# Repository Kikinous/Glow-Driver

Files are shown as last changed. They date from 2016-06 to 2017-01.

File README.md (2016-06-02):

# Glow-Driver
Glow Driver for model engine with current sensor

Blog thread: http://www.eevblog.com/forum/projects/improving-glow-plug-drive-design-for-rc-plane-radial-engine/

* eagle file
  - digikey bill of material
  - OSH park PCB manufacture details

* attiny code
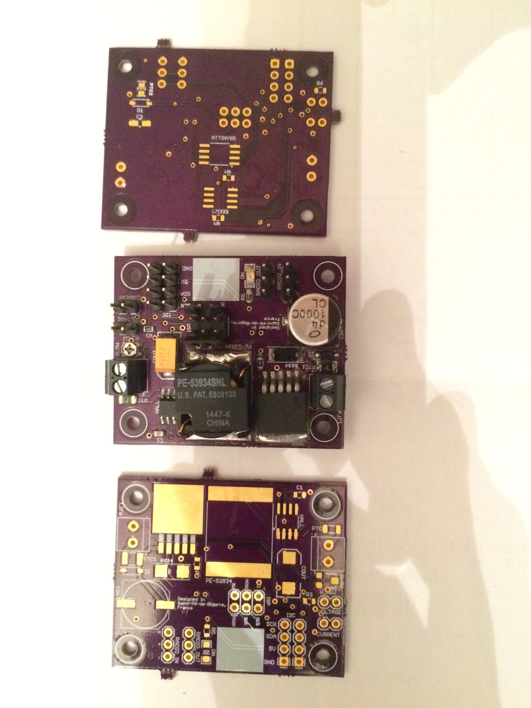
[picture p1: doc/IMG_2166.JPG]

* Main computer board
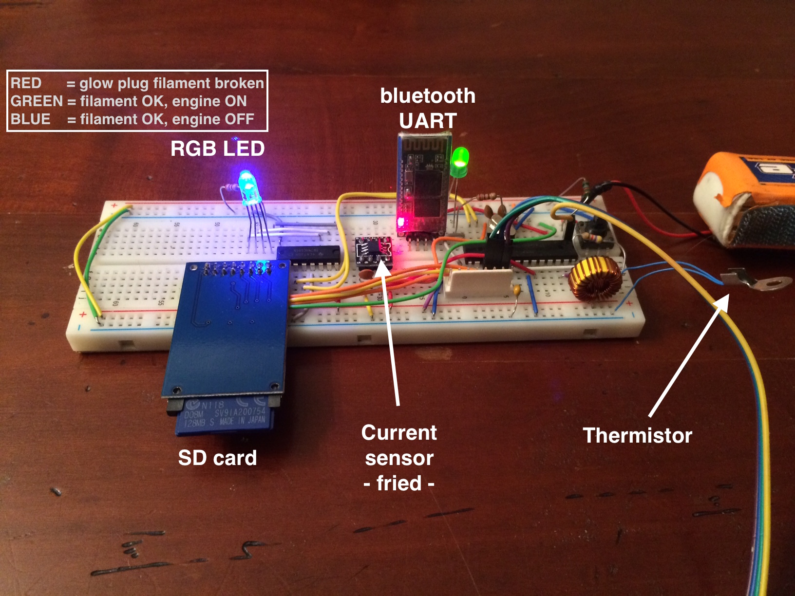
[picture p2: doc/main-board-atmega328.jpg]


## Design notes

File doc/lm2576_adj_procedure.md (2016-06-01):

# LM2576-ADJ

# Given
Vout = 1.5V
Vin = 9.9V
Iload = 1.5A (Rload = 1 ohm)

#Programming output voltage
Vout = Vref ( 1+R2/R1) Vref = 1.23V

R2 = R1 (Vout/Vref -1) avec 1k < R1 < 5k
pot : R2 + R1 = 10k
R1 = 8.2k
R2 = 1.8k

# induductor selection
* E.t
E.t = (Vin-Vout)*(Vout/Vin)*(1000/52)  
E.t = (9.9-1.5)*(1.5/9.9)*(1000/52)  
E.t = 24 V/us
* figure 27
E.t = 24 & I = 1.5A => L = 47 - 68 uH
inductance choisie 64uH 5A

# output capacitor
Cout > 13,300 * Vin /(Vout * L[uH]) [uF]
but may be much larger
Cout > 13,300 * 9.9 /(1.5  * 64) [uF]
Cout > 1372 uF
J'avais 680uF, je mets 2000uF

##################################################################

LM2576 - LM2577 up converter : error

# Distronics : TO220-5 LM2596T-ADJ 
## Programming voltage
E.t = (Vin - Vout - Vsat ) . ( Vout + Vd ) / (Vin - Vsat + Vd) . (1000 / 150) [V.us]
E.t = 9.4 V.us
--> 15uH , inductor code = L34  (check table 3)
L34
L = 15
I = 3.40
Through hole or surface mount

## Output capacitor
C = 10nF tantalium or electrolitic - table 2

## Feedforward capacitor 
C = 10nF ceramic - table 2

## Catch diode
Schottky diodes : 5 A rating 

## Input capacitor 
look for RMS current to avoid heating : big capacitor qui chauffe pas

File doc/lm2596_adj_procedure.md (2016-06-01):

# LM2595-ADJ

# Given
Vout = 1.2V
Vin = 9.9V
Iload = 2.5A (Rload = 0.5 Ohm)

#Programming output voltage
Vout = Vref ( 1+R2/R1) Vref = 1.23V

R2 = R1 (Vout/Vref -1) avec 1k < R1 < 5k
pot : R2 + R1 = 10k
R1 = 8.2k
R2 = 1.8k

# induductor selection
* E.t
E.t = (Vin-Vout-Vsat) * (Vout+Vd)/(Vin-Vsat+Vd) * 1000 / 150kHz  (V.us)
Vsat = 1.16V
Vd   = 0.5V
E.t = (9.9-1.2-0.5) * (1.2+0.5)/(9.9-1.16+0.5) * 1000/150
    = 10.06 (V.us)
* figure 24 : 
L = 15uH et inductor code = L34
brand
Schott / hole    = 67148400   =
Schott / SMT     = 67148790   =
Pulse eng / hole = PE-53934   =
Pulse eng / SMT  = PE-53934-S = digikey# 553-1417-ND = 2.17
 
# output capacitor
* Table 2
  Vout ~ 2V --> 330uF/6.3V AVX TPS Series       = digikey 478-9193-1-ND = 1.8 EUR
                470uF/4V   Sprague 595D Series  = no stock

# Catch diode
SK34 - 4->6 Amp  = digikey SK34A-TPCT-ND = 0.5 EUR

#Input Capacitor (CIN)
1000uF/16V                      = digikey P15087CT-ND = 0.9 EUR

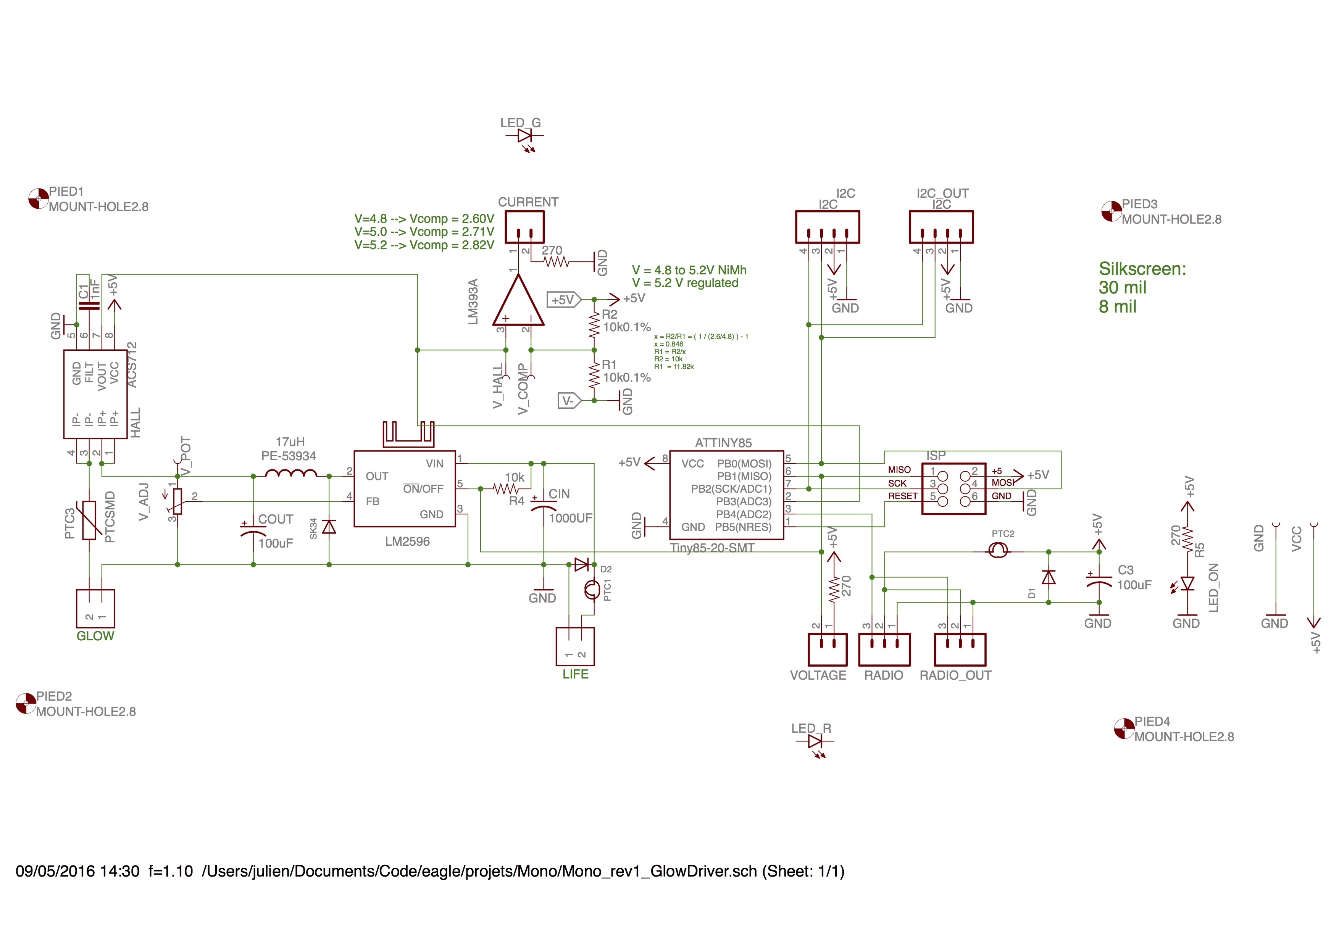
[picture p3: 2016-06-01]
Parts_Manufacture_Orders/Mono_rev1_GlowDriver_schematic.jpg

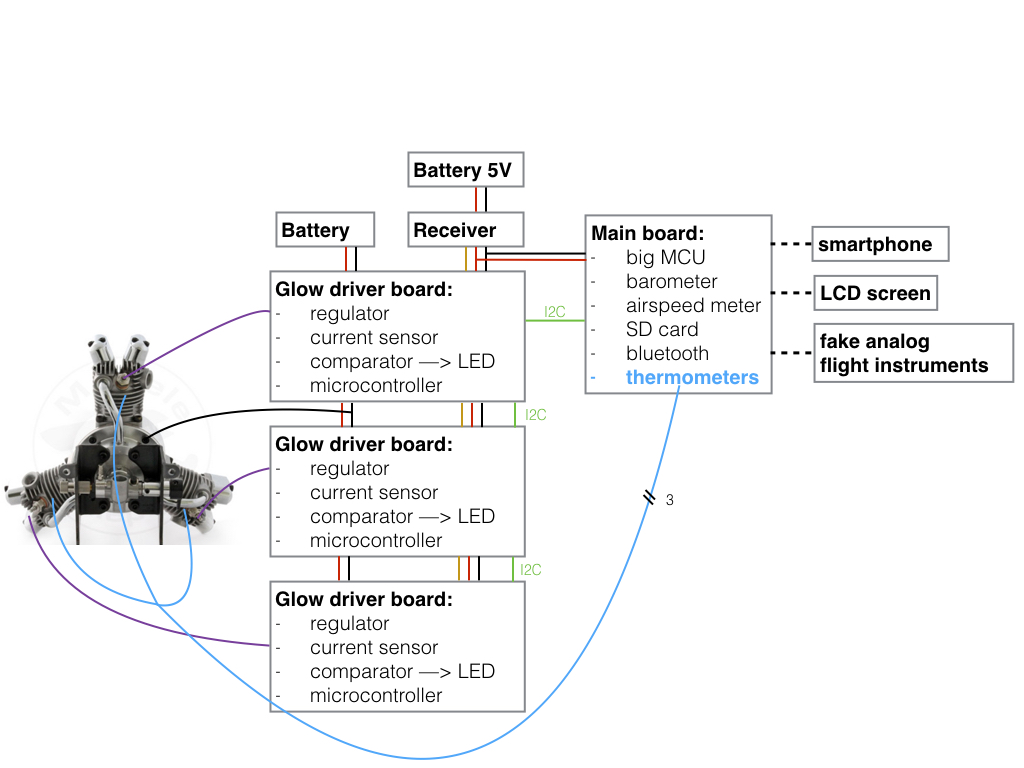
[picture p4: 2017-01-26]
doc/Big-picture.jpg

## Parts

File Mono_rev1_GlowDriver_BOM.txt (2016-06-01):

Partlist exported from /Users/julien/Documents/Code/eagle/projets/Mono/Mono_rev1_GlowDriver.sch at 09/05/2016 11:24

Part      Value                  Device                  Package     Description                                                             DIGIKEY            MF                     MPN              OC_FARNELL OC_NEWARK PROD_ID   VALUE        
ATTINY85  Tiny85-20-SMT          ATTINY45TINY85-20-SMT   SO08-EIAJ   Atmel 8-pin 2/4/8kB flash uC                                            ATTINY85-20SU-ND                                                                IC-09092  Tiny85-20-SMT
C1        1nF                    CAP0805                 0805        Capacitor                                                               490-11585-1-ND                                                                                         
C3        100uF                  CPOL-USCT3216           CT3216      POLARIZED CAPACITOR, American symbol                                    478-1777-1-ND                                                                                          
CIN       1000UF                 CPOL-USG                PANASONIC_G POLARIZED CAPACITOR, American symbol                                    493-3930-1-ND                                                                                          
COUT      100uF                  100UF-10V-10%(TANT)     EIA7343     CAP-07890                                                               478-9193-1-ND                                                                   CAP-07890 100uF        
CURRENT                          M02PTH                  1X02        Standard 2-pin 0.1" header. Use with                                    S1011EC-40-ND                                                                                          
D1                               DIODESOD-123            SOD-123     Diode                                                                   1N4150W-E3-08CT-ND                                                                                     
D2                               DIODESOD-123            SOD-123     Diode                                                                   1N4150W-E3-08CT-ND                                                                                     
GLOW      1X2-3.5MM              1X2-3.5MM               1X2-3.5MM   3.5mm Terminal block                                                    ED1514-ND                                                                                              
GND       TEST-POINTTP_15TH_THRU TEST-POINTTP_15TH_THRU  TP_15TH     Bare copper test points for troubleshooting or ICT                                                                                                                             
HALL      ACS712                 ACS712                  SO08        Hall-effect-based isolated linear current sensor                        620-1189-1-ND                                                                   IC-08964               
I2C       I2C                    M04PTH                  1X04        Header 4                                                                S1011EC-40-ND                                                                                          
I2C_OUT   I2C                    M04PTH                  1X04        Header 4                                                                S1011EC-40-ND                                                                                          
ISP       AVR_SPI_PRG_6PTH       AVR_SPI_PRG_6PTH        2X3         AVR ISP 6 Pin                                                           609-2423-ND                                                                                            
KK1       D0A-L                  D0A-L                   D02A-L      HEATSINK                                                                AE10837-ND                                                                                             
LED_G                            LED5MM                  LED5MM      LEDs                                                                    67-1098-ND                                                                                             
LED_ON                           LED-GREEN1206           LED-1206    Various green LEDs                                                      404-1046-1-ND                                                                   DIO-00862 GREEN        
LED_R                            LED5MM                  LED5MM      LEDs                                                                    67-1105-ND                                                                                             
LIFE      1X2-3.5MM              1X2-3.5MM               1X2-3.5MM   3.5mm Terminal block                                                    ED1514-ND                                                                                              
LM393     LM393D                 LM393D                  SO08        COMPARATOR                                                              296-1015-5-ND                                                                                          
LM2596    LM2596S                LM2596S                 TO263-5     SIMPLE SWITCHER® Power Converter 150 kHz 3A Step-Down Voltage Regulator 296-35399-1-ND     NATIONAL SEMICONDUCTOR LM2596S-ADJ/NOPB 9494367    41K3842                          
PE-53934  17uH                   PE-53934                LCI-44                                                                              553-1417-ND                                                                                            
PIED1     MOUNT-HOLE2.8          MOUNT-HOLE2.8           2,8         MOUNTING HOLE with drill center marker                                                                                                                                         
PIED2     MOUNT-HOLE2.8          MOUNT-HOLE2.8           2,8         MOUNTING HOLE with drill center marker                                                                                                                                         
PIED3     MOUNT-HOLE2.8          MOUNT-HOLE2.8           2,8         MOUNTING HOLE with drill center marker                                                                                                                                         
PIED4     MOUNT-HOLE2.8          MOUNT-HOLE2.8           2,8         MOUNTING HOLE with drill center marker                                                                                                                                         
PTC1      750MA-6V               SMD-PPTC-750MA-6V(1210) F1210       307010010                                                               F5766CT-ND                                SMD1210R075SF                                   750MA-6V     
PTC2      100A-6V                SMD PPTC 100A-6V(0805)  F0805       307010046                                                               507-1811-1-ND                             SMD0805R100S                                    100A-6V      
PTC3      PTCSMD                 PTCSMD                  PTC-1206    Resettable Fuse PTC                                                     RF2305-000CT-ND                                                                 RES-11150              
R1        10k0.1%                RESISTOR0805-RES        0805        Resistor                                                                P10KACT-ND                                                                                             
R2        10k0.1%                RESISTOR0805-RES        0805        Resistor                                                                P10KACT-ND                                                                                             
R3        270                    RESISTOR0805-RES        0805        Resistor                                                                P270ACT-ND                                                                                             
R4        10k                    RESISTOR0805-RES        0805        Resistor                                                                P10KACT-ND                                                                                             
R5        270                    RESISTOR0805-RES        0805        Resistor                                                                P270ACT-ND                                                                                             
R6        270                    RESISTOR0805-RES        0805        Resistor                                                                P270ACT-ND                                                                                             
RADIO                            M03PTH                  1X03        Header 3                                                                S1011EC-40-ND                                                                                          
RADIO_OUT                        M03PTH                  1X03        Header 3                                                                S1011EC-40-ND                                                                                          
SK34                             DIODESMA                SMADIODE    Diode                                                                   SK34A-TPCT-ND                                                                                          
VCC       TEST-POINTTP_15TH_THRU TEST-POINTTP_15TH_THRU  TP_15TH     Bare copper test points for troubleshooting or ICT                                                                                                                             
VOLTAGE                          M02PTH                  1X02        Standard 2-pin 0.1" header. Use with                                    S1011EC-40-ND                                                                                          
V_ADJ                            TRIMPOTTC33X            TC33X       SMT trimmer potentiometer part number TC33X                             TC33X-103ECT-ND                                                                                        
V_COMP    TEST-POINTTP_15TH_THRU TEST-POINTTP_15TH_THRU  TP_15TH     Bare copper test points for troubleshooting or ICT                                                                                                                             
V_HALL    TEST-POINTTP_15TH_THRU TEST-POINTTP_15TH_THRU  TP_15TH     Bare copper test points for troubleshooting or ICT                                                                                                                             
V_POT     TEST-POINTTP_15TH_THRU TEST-POINTTP_15TH_THRU  TP_15TH     Bare copper test points for troubleshooting or ICT

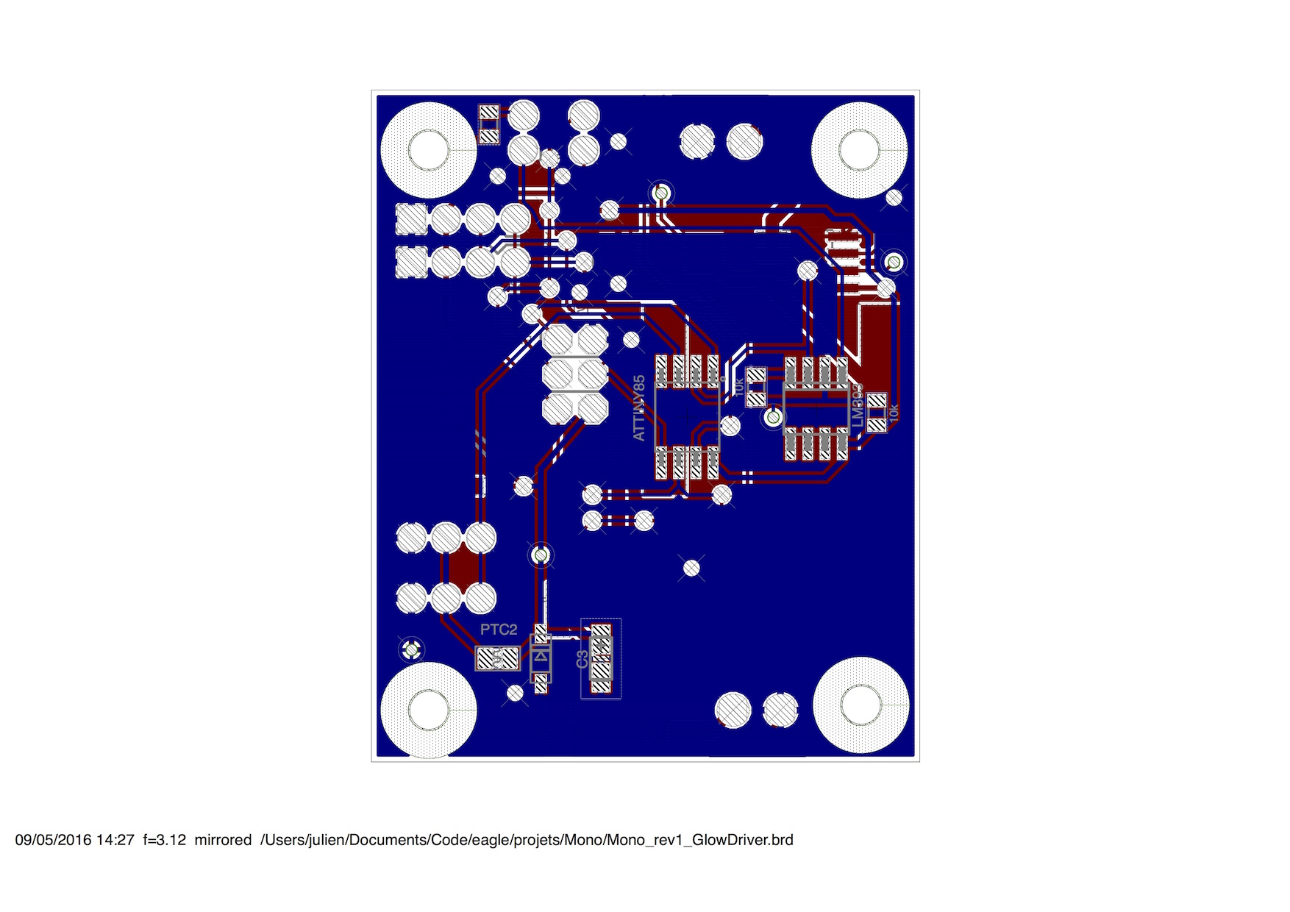
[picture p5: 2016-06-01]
Parts_Manufacture_Orders/Mono_rev1_GlowDriver_down.jpg

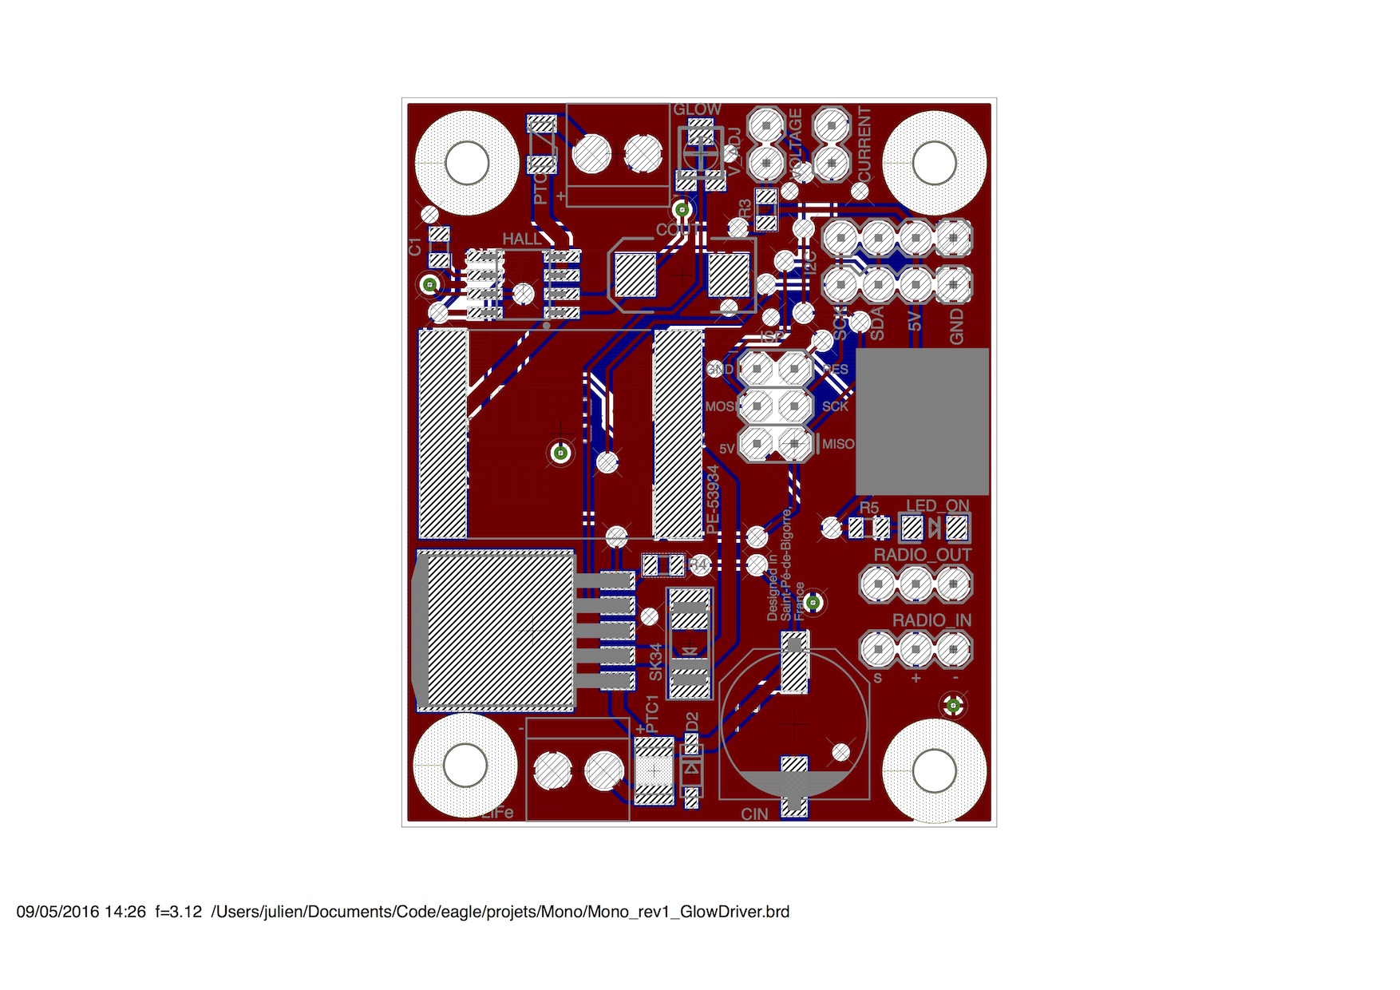
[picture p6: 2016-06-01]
Parts_Manufacture_Orders/Mono_rev1_GlowDriver_up.jpg

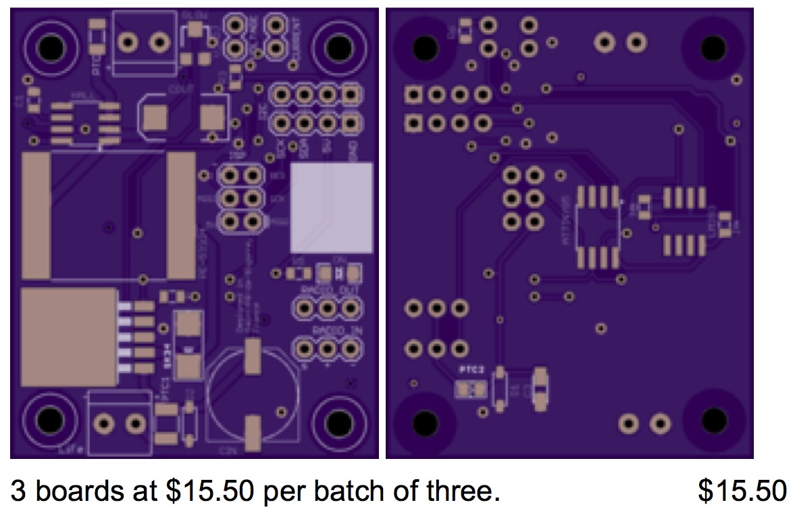
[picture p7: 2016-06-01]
Parts_Manufacture_Orders/PCB_OSH Park.jpg

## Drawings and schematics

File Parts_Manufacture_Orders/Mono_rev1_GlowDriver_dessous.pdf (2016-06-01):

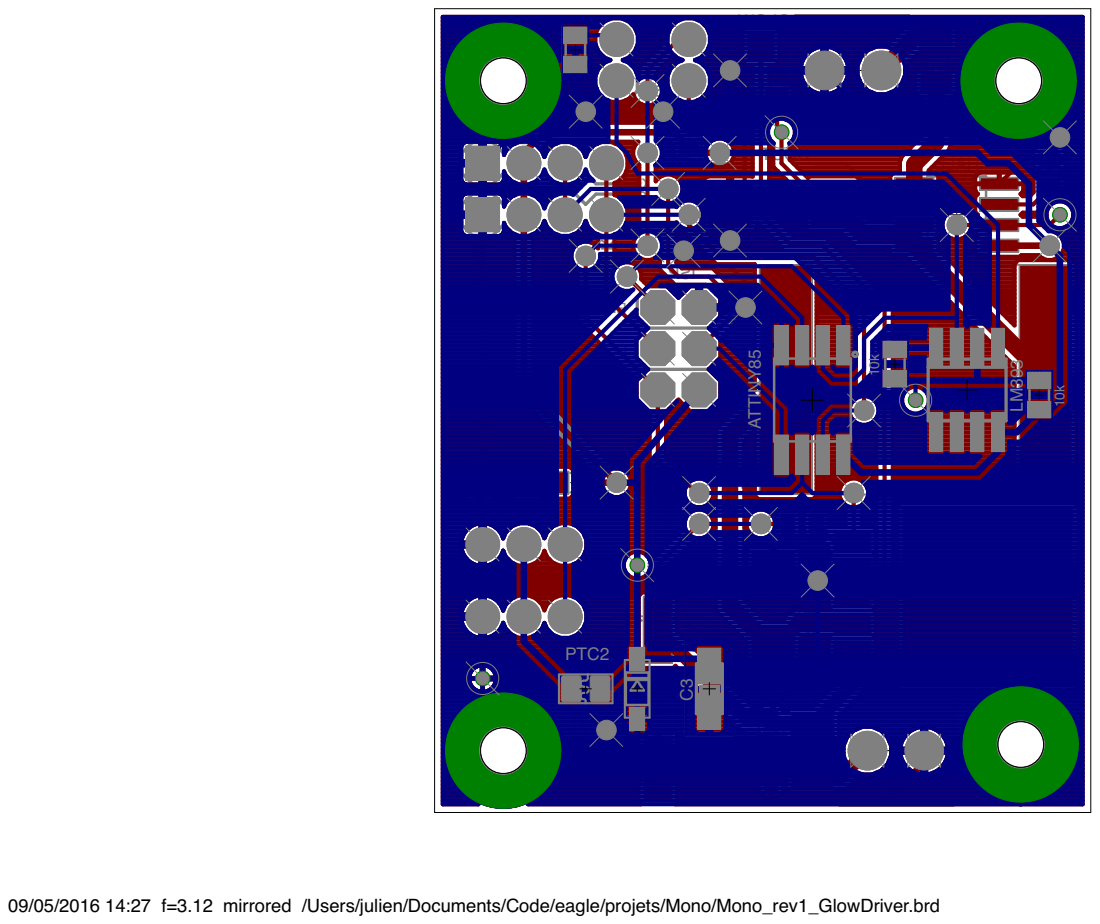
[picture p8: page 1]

Designed in Saint-Pé-de-Bigorre, France

09/05/2016 14:27 f=3.12 mirrored /Users/julien/Documents/Code/eagle/projets/Mono/Mono_rev1_GlowDriver.brd

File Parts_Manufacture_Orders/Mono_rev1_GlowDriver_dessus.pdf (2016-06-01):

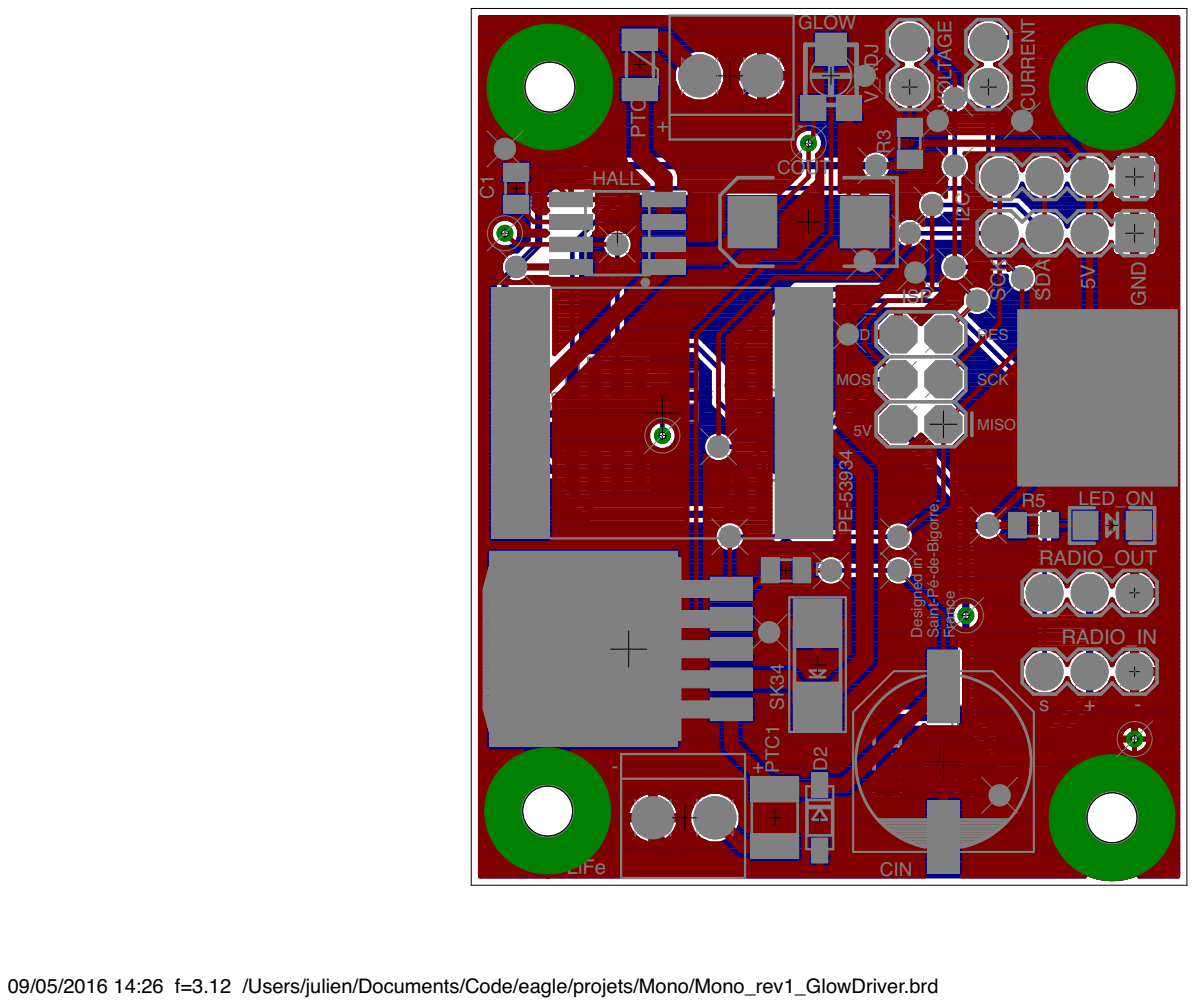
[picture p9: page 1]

09/05/2016 14:26 f=3.12 /Users/julien/Documents/Code/eagle/projets/Mono/Mono_rev1_GlowDriver.brd

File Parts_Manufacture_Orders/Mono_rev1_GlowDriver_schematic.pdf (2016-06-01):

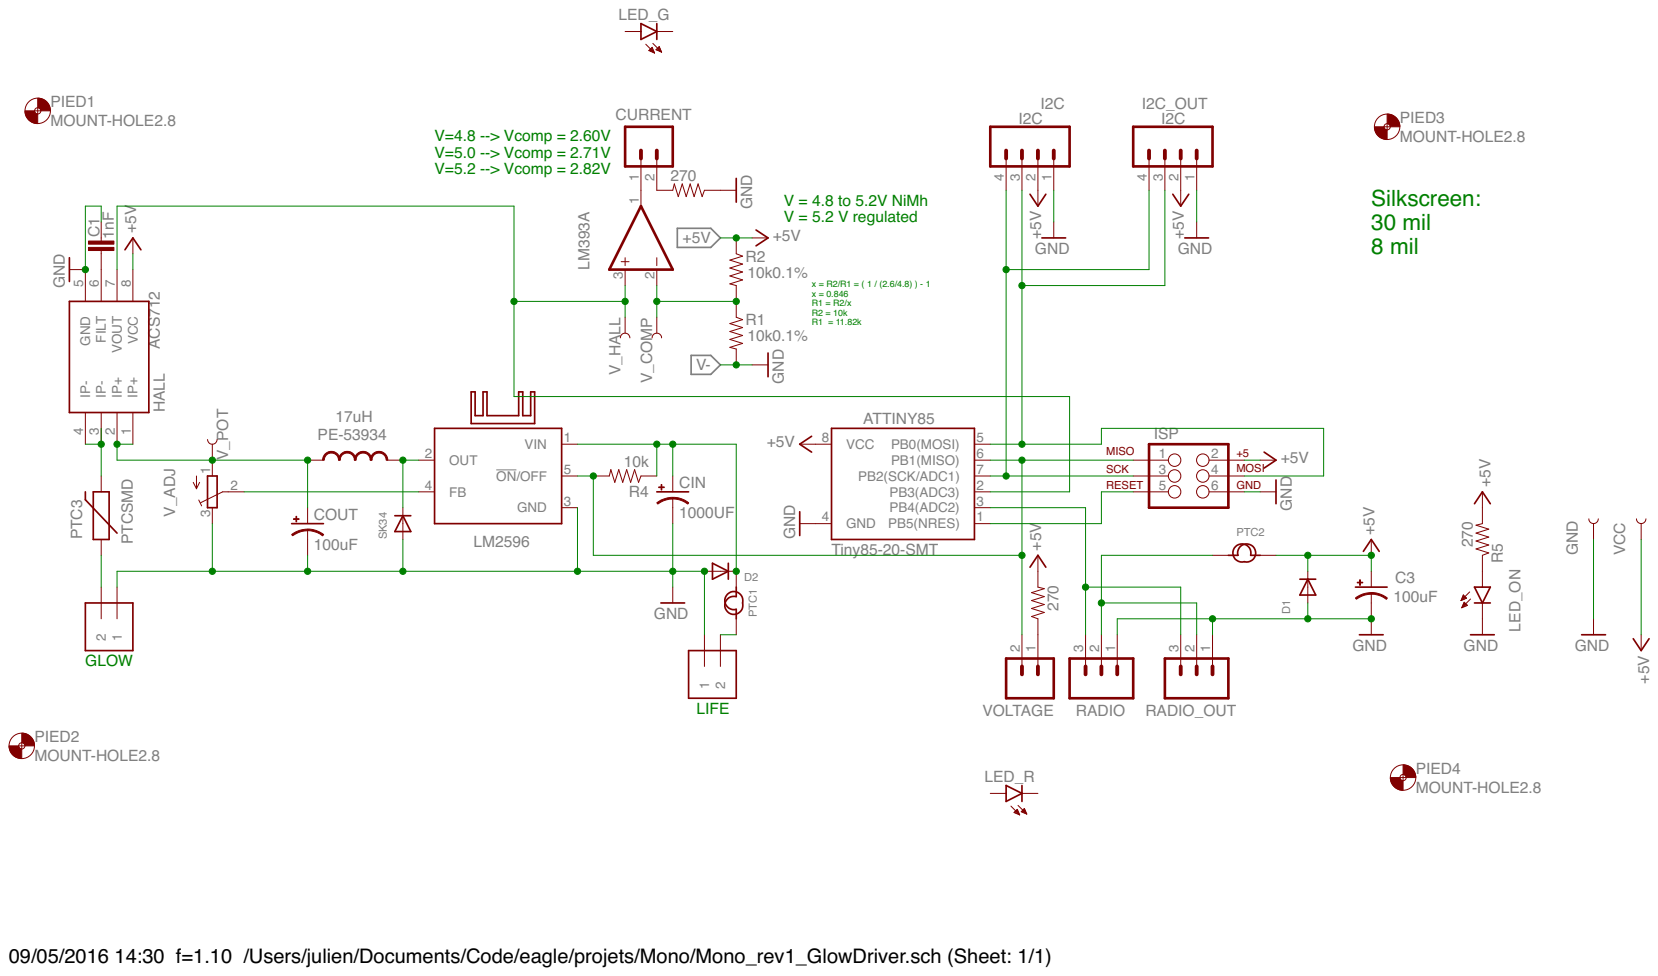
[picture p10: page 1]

09/05/2016 14:30 f=1.10 /Users/julien/Documents/Code/eagle/projets/Mono/Mono_rev1_GlowDriver.sch (Sheet: 1/1)

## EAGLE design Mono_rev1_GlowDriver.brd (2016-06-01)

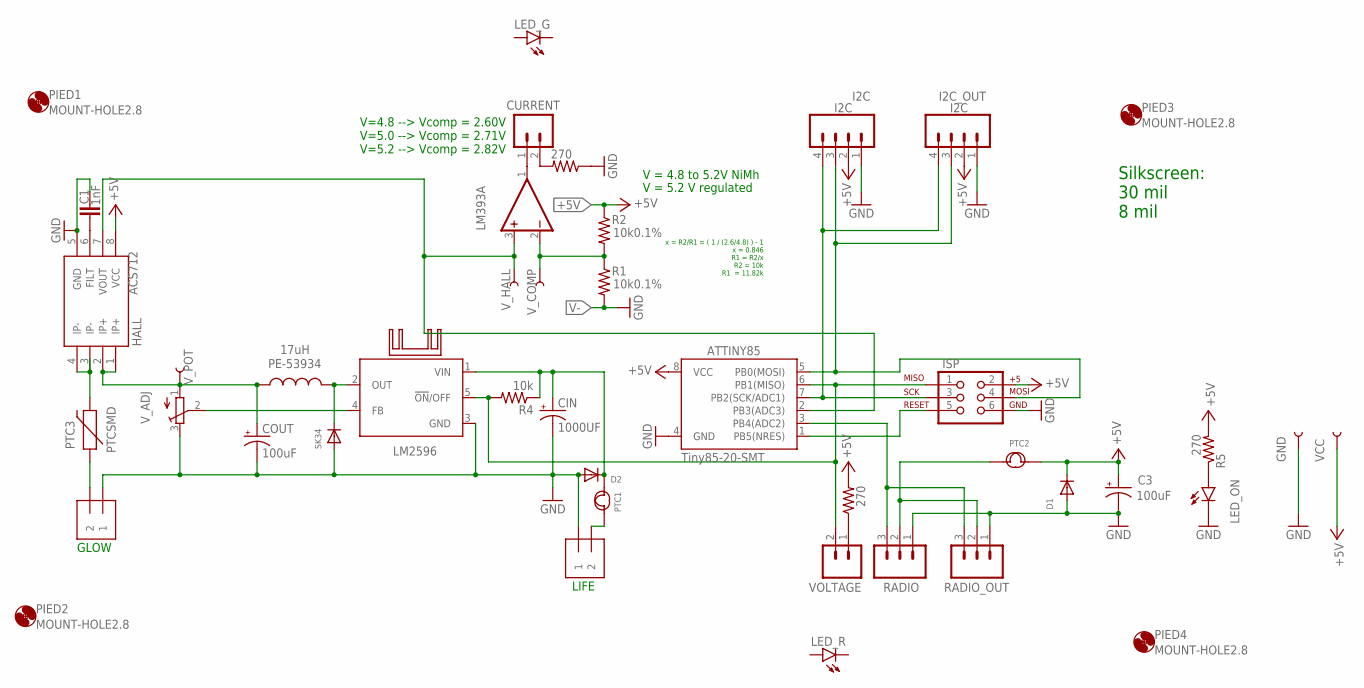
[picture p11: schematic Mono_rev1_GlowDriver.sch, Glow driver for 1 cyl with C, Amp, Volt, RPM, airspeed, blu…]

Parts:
ATTINY85: Tiny85-20-SMT; SO08-EIAJ; DIGIKEY ATTINY85-20SU-ND
C1: 1nF; 0805; DIGIKEY 490-11585-1-ND
C3: 100uF; CT3216; DIGIKEY 478-1777-1-ND
CIN: 1000UF; PANASONIC_G; DIGIKEY 493-3930-1-ND
COUT: 100uF; EIA7343; DIGIKEY 478-9193-1-ND
CURRENT: M02PTH; 1X02; DIGIKEY S1011EC-40-ND
D1, D2: DIODESOD-123; SOD-123; DIGIKEY 1N4150W-E3-08CT-ND
GLOW: 1X2-3.5MM; DIGIKEY ED1514-ND
GND: TEST-POINTTP_15TH_THRU; TP_15TH
HALL: ACS712; SO08; DIGIKEY 620-1189-1-ND
I2C, I2C_OUT: I2C; 1X04; DIGIKEY S1011EC-40-ND
ISP: AVR_SPI_PRG_6PTH; 2X3; DIGIKEY 609-2423-ND
KK1: D0A-L; D02A-L; DIGIKEY AE10837-ND
LED_G: LED5MM
LED_ON: LED-GREEN1206; LED-1206; DIGIKEY 404-1046-1-ND
LED_R: LED5MM
LIFE: 1X2-3.5MM; DIGIKEY ED1514-ND
LM393: LM393D; SO08; DIGIKEY 296-1015-5-ND
LM2596: LM2596S; TO263-5; DIGIKEY 296-35399-1-ND
PE-53934: 17uH; LCI-44; DIGIKEY 553-1417-ND
PIED1, PIED2, PIED3, PIED4: MOUNT-HOLE2.8; 2,8
PTC1: 750MA-6V; F1210; DIGIKEY F5766CT-ND
PTC2: 100A-6V; F0805; DIGIKEY 507-1811-1-ND
PTC3: PTCSMD; PTC-1206; DIGIKEY RF2305-000CT-ND
R1, R2: 10k0.1%; 0805; DIGIKEY P10KACT-ND
R3, R5, R6: 270; 0805; DIGIKEY P270ACT-ND
R4: 10k; 0805; DIGIKEY P10KACT-ND
RADIO: M03PTH; 1X03; DIGIKEY S1011EC-40-ND
RADIO_OUT: M03PTH; 1X03; DIGIKEY S1011EC-40-ND
SK34: DIODESMA; SMADIODE; DIGIKEY SK34A-TPCT-ND
VCC: TEST-POINTTP_15TH_THRU; TP_15TH
VOLTAGE: M02PTH; 1X02; DIGIKEY S1011EC-40-ND
V_ADJ: TRIMPOTTC33X; TC33X; DIGIKEY TC33X-103ECT-ND
V_COMP: TEST-POINTTP_15TH_THRU; TP_15TH
V_HALL: TEST-POINTTP_15TH_THRU; TP_15TH
V_POT: TEST-POINTTP_15TH_THRU; TP_15TH

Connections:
+5V: ATTINY85.8 (VCC), C3.+, D1.C, HALL.8 (VCC), I2C.2, I2C_OUT.2, ISP.2, LM393.8 (V+), PTC2.2, R2.1, R3.2, R5.2, VCC.P$1
GND: ATTINY85.4 (GND), C1.1, C3.-, CIN.-, COUT.C (-), D1.A, D2.A, GLOW.1, GND.P$1, HALL.5 (GND), I2C.1, I2C_OUT.1, ISP.6, LED_ON.C, LIFE.1, LM2596.3 (GND), R6.1, RADIO.1, RADIO_OUT.1, SK34.A, V_ADJ.3 (E)
unnamed: R3.1, VOLTAGE.1
unnamed: ATTINY85.3 (PB4(ADC2)), RADIO.3, RADIO_OUT.3
unnamed: ATTINY85.7 (PB2(SCK/ADC1)), I2C.4, I2C_OUT.4, ISP.3
unnamed: ATTINY85.2 (PB3(ADC3)), HALL.7 (VOUT), LM393.3 (+IN), V_HALL.P$1
unnamed: LED_ON.A, R5.1
unnamed: HALL.3 (IP-), HALL.4 (IP-), PTC3.2
unnamed: CURRENT.2, R6.2
unnamed: CURRENT.1, LM393.1 (OUT)
unnamed: LM2596.2 (OUT), PE-53934.P$2 (2), SK34.C
unnamed: GLOW.2, PTC3.1
unnamed: LIFE.2, PTC1.1
unnamed: LM2596.4 (FB), V_ADJ.2 (S)
unnamed: CIN.+, D2.C, LM2596.1 (VIN), PTC1.2, R4.1
unnamed: PTC2.1, RADIO.2, RADIO_OUT.2
unnamed: LM393.2 (-IN), R1.1, R2.2, V_COMP.P$1
unnamed: ATTINY85.5 (PB0(MOSI)), I2C.3, I2C_OUT.3, ISP.4
unnamed: ATTINY85.6 (PB1(MISO)), ISP.1, LM2596.5 (!ON!/OFF), R4.2, VOLTAGE.2
unnamed: C1.2, HALL.6 (FILT)
unnamed: ATTINY85.1 (PB5(NRES)), ISP.5
POT10K: COUT.A (+), HALL.1 (IP+), HALL.2 (IP+), PE-53934.P$1 (1), V_ADJ.1 (A), V_POT.P$1
V-: LM393.4 (V-), R1.2

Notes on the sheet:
GLOW
LIFE
V = 5.2 V regulated
V = 4.8 to 5.2V NiMh
x = R2/R1 = ( 1 / (2.6/4.8) ) - 1 x = 0.846 R1 = R2/x R2 = 10k R1 = 11.82k
V=4.8 --> Vcomp = 2.60V V=5.0 --> Vcomp = 2.71V V=5.2 --> Vcomp = 2.82V
Silkscreen: 30 mil 8 mil

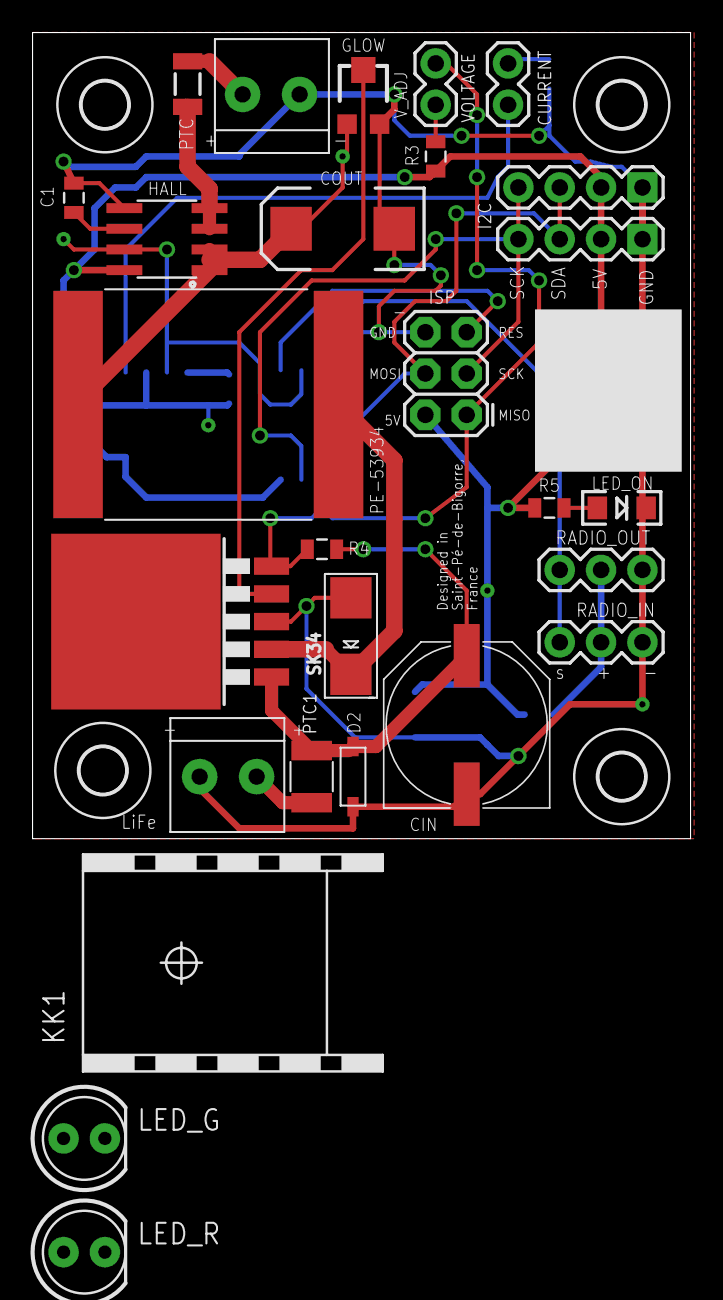
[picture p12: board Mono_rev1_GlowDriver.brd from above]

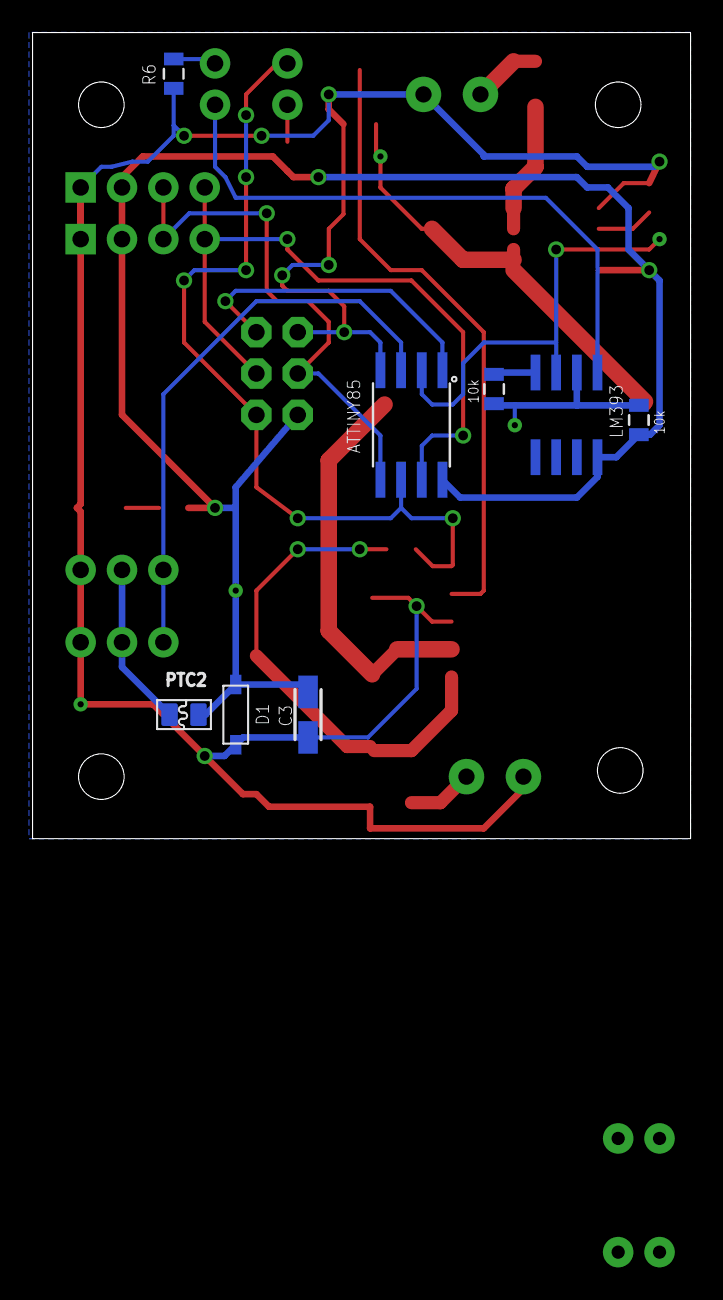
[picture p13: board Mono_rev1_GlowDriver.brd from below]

Board: 2 copper layers, 40.4 x 49.5 mm, 44 parts (8 on the bottom side), 23 nets.

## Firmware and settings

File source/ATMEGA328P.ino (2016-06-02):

/*
    Julien Borghetti - March 2016
    Revision Avril 2016

    Programmed for an ATMEGA328P
    BOARD picture:
    https://raw.githubusercontent.com/Kikinous/Glow-Driver/master/doc/main-board-atmega328.jpg

    - Measure temperature (thermistor & ADC & curve fit)
    - write data in SD card
    - send data over bluetooth BLE
    - print data to nokia 5110
    - switch LED red, green, blue when the data is respectivly low, good, high
    - current sensor doesn't work yet
*/

// ACTIVATE DEBUG MESSAGES & TEST CODE
#define DEBUG
#ifdef DEBUG
    #define DEBUG_PRINT(x)  Serial.println (x)
    //#define DEBUG_SDcard
#else
    #define DEBUG_PRINT(x)
#endif


// SD LIBRARY:
#ifdef DEBUG_SDcard
    #include <SPI.h>
#endif
#include <SD.h>
Sd2Card card;
SdVolume volume;
SdFile root;
File myFile;
#define SDcardCHIPSELECT 2 //PD2 is free in Radial3_rev1 eagle
char filename[] = "LOGGER00.csv";


// I2C library
//#include <Wire.h>


// SCREEN LIBRARY
// http://forum.arduino.cc/index.php?topic=176794
#include <SPI.h>
#include "PCD8544_SPI.h"
PCD8544_SPI lcd;


// VARISTOR voltage divider and coefficients (check curve fitting python script)
#define SERIESRESISTOR 4630
#define THERMISTORNOMINAL 10000
#define BCOEFFICIENT 4005.58
#define TEMPERATURENOMINAL 298.26
#define THERMISTORPIN A3
#define THERMISTOR_LOW_THRESHOLD 27.0   // Celcius
#define THERMISTOR_HIGH_THRESHOLD 29.0  // Celcius


// CURRENT SENSOR
#define CURRENTSENSORPIN A0
#define COEFFICIENT_mVperAmp 185
#define COEFFICIENT_ACSoffset 2500


// SHIFT REGISTER
#define HC595_latchPin 7 //Pin connected to latch pin (ST_CP) of HC595
#define HC595_clockPin 6 //Pin connected to clock pin (SH_CP) of HC595
#define HC595_dataPin 5  //Pin connected to Data in   (DS) of HC595


// LOOP TIMING
#define LOOP_TIMING_ADC 500
unsigned long millis_ADC = 0;
#define LOOP_TIMING_SDcard 1000
unsigned long millis_SDcard = 0;


// LED INDICATOR STATES
int Etat_bougie = 1;  // 1 : 0   < amp < 2    --> red   pin 1
                      // 3 : 2   < amp < 2.5  --> green pin 3
                      // 2 : 2.5 < amp        --> blue  pin 2
float temperature = 0;
float courant     = 0;


/////////////////////////////// MAIN FUNCTIONS ///////////////////////////////



void setup() {

    //Display
    lcd.begin(); // 14X6 characters
    //           01234567890123
    lcd.print(F("              "));
    lcd.print(F("   FLIGHT     "));
    lcd.print(F("              "));
    lcd.print(F(" INSTRUMENTS  "));

    // SHIFT REGISTER
    pinMode(HC595_latchPin, OUTPUT);
    pinMode(HC595_dataPin, OUTPUT);
    pinMode(HC595_clockPin, OUTPUT);
    registerWrite(1,LOW);
    delay(1000);

    // SIGNIFY DEBUG MODE
#ifdef DEBUG
    for (int i=0; i <= 9; i++){
        registerWrite(1,HIGH);
        delay(100);
        registerWrite(1,LOW);
        delay(100);
    }
#endif

    // UART
    Serial.begin(9600);
    Serial.println("\nConnection serial etablie");

    // SD CARD
#ifdef DEBUG_SDcard
    SD_card_test();
#endif
    SDcard_init();

    // UNIT LOOP scheduler
    millis_ADC    = millis();
    millis_SDcard = millis();
}





void loop() {
    if ( millis() - millis_ADC >= LOOP_TIMING_ADC ){
        String message;
        size_t len;
        millis_ADC  = millis();
        temperature = lire_temperature();
        courant     = lire_courant();
        message    = "T=" + String(int(temperature)) + " I=" + String(courant);
        //char message_lcd[84];
        //message.toCharArray(message_lcd,84);
        lcd.clear();
        lcd.print(message);
        Serial.println(message);

        Etat_bougie = set_LED_indicator(Etat_bougie,temperature);
    }
    if ( millis() - millis_SDcard >= LOOP_TIMING_SDcard ){
        millis_SDcard = millis();
        myFile        = SD.open(filename, FILE_WRITE);
        if (myFile) {
            myFile.print(courant);
            myFile.print(",");
            myFile.println(temperature);
            myFile.close();
        }
    }
}







/////////////////////////////// OTHER FUNCTIONS ///////////////////////////////

void SDcard_init(){
    // On the Ethernet Shield, CS is pin 4. It's set as an output by default.
    // Note that even if it's not used as the CS pin, the hardware SS pin
    // (10 on most Arduino boards, 53 on the Mega) must be left as an output
    // or the SD library functions will not work.
    //pinMode(10, OUTPUT);
    if (!SD.begin(SDcardCHIPSELECT)) Serial.println("SD Card initialization failed!");
    // create a new file
    for (uint8_t i = 0; i < 100; i++) {
        filename[6] = i/10 + '0';
        filename[7] = i%10 + '0';
        if (! SD.exists(filename)) {
            // only open a new file if it doesn't exist
            myFile = SD.open(filename, FILE_WRITE);
            break;  // leave the loop!
        }
    }
    if (! myFile) Serial.println("couldnt create file");
    Serial.print("Logging to: ");
    Serial.println(filename);
    if (myFile) {
        myFile.print("Courant");
        myFile.print(",");
        myFile.println("Temperature");
        myFile.close();
        Serial.println("SD card initialization done.");
    }
}


int set_LED_indicator(int Etat, float temperature){
    registerWrite(Etat, LOW);
    if( temperature < THERMISTOR_LOW_THRESHOLD ){
        Etat = 1;
        registerWrite(Etat, HIGH);
    } else if( (THERMISTOR_LOW_THRESHOLD <= temperature) && (temperature < THERMISTOR_HIGH_THRESHOLD) ){
        Etat = 3;
        registerWrite(Etat, HIGH);
    } else{
        Etat = 2;
        registerWrite(Etat, HIGH);
    }
    return Etat;
}


float lire_temperature() {
    // convert the varistor value to temperature
    float reading;
    reading = analogRead(THERMISTORPIN);
    reading = (1023 / reading)  - 1;
    reading = SERIESRESISTOR / reading;
    //Steinhart-Hart equation (simplified - voir curve fit en python)
    // (1/T) = (1/T0) + 1/B ln (R/Ro)
    float steinhart;
    steinhart = reading / THERMISTORNOMINAL;     // (R/Ro)
    steinhart = log(steinhart);                  // ln(R/Ro)
    steinhart /= BCOEFFICIENT;                   // 1/B * ln(R/Ro)
    steinhart += 1.0 / (TEMPERATURENOMINAL);     // + (1/To)
    steinhart = 1.0 / steinhart;                 // Invert
    steinhart -= 273.15;                         // convert to C
    return steinhart;
}


float lire_courant() {
   float reading;
   reading = analogRead(CURRENTSENSORPIN);
   reading = (reading / 1023.0) * 5000;     // Gets you mV
   reading = ((reading  - COEFFICIENT_ACSoffset) / COEFFICIENT_mVperAmp);
   return reading;
}


void registerWrite(int whichPin, int whichState) {               // This method sends bits to the shift register:
    byte bitsToSend = 0;                                           // the bits you want to send
    digitalWrite(HC595_latchPin, LOW);                             // turn off the output so the pins don't light up while you're shifting bits:
    bitWrite(bitsToSend, whichPin, whichState);                    // turn on the next highest bit in bitsToSend:
    shiftOut(HC595_dataPin, HC595_clockPin, MSBFIRST, bitsToSend); // shift the bits out:
    digitalWrite(HC595_latchPin, HIGH);                            // turn on the output so the LEDs can light up:
}



///////////////////////////////     DEBUG       ///////////////////////////////

#ifdef DEBUG_SDcard
void SD_card_test(){
    Serial.print("\nInitializing SD card...");

    // we'll use the initialization code from the utility libraries
    // since we're just testing if the card is working!
    if (!card.init(SPI_HALF_SPEED, SDcardCHIPSELECT)) {
        Serial.println("initialization failed. Things to check:");
        Serial.println("* is a card inserted?");
        Serial.println("* is your wiring correct?");
        Serial.println("* did you change the SDcardCHIPSELECT pin to match your shield or module?");
        return;
    } else {
        Serial.println("Wiring is correct and a card is present.");
    }

    // print the type of card
    Serial.print("\nCard type: ");
    switch (card.type()) {
         case SD_CARD_TYPE_SD1:
             Serial.println("SD1");
             break;
         case SD_CARD_TYPE_SD2:
             Serial.println("SD2");
             break;
         case SD_CARD_TYPE_SDHC:
             Serial.println("SDHC");
             break;
         default:
             Serial.println("Unknown");
    }

    // Now we will try to open the 'volume'/'partition' - it should be FAT16 or FAT32
    if (!volume.init(card)) {
        Serial.println("Could not find FAT16/FAT32 partition.\nMake sure you've formatted the card");
        return;
    }


    // print the type and size of the first FAT-type volume
    uint32_t volumesize;
    Serial.print("\nVolume type is FAT");
    Serial.println(volume.fatType(), DEC);
    Serial.println();

    volumesize = volume.blocksPerCluster();       // clusters are collections of blocks
    volumesize *= volume.clusterCount();          // we'll have a lot of clusters
    volumesize *= 512;                            // SD card blocks are always 512 bytes
    Serial.print("Volume size (bytes): ");
    Serial.println(volumesize);
    Serial.print("Volume size (Kbytes): ");
    volumesize /= 1024;
    Serial.println(volumesize);
    Serial.print("Volume size (Mbytes): ");
    volumesize /= 1024;
    Serial.println(volumesize);


    Serial.println("\nFiles found on the card (name, date and size in bytes): ");
    root.openRoot(volume);

    // list all files in the card with date and size
    root.ls(LS_R | LS_DATE | LS_SIZE);
}
#endif

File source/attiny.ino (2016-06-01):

/*
   Julien Borghetti - March 2016
   Revision Avril 2016 - eagle file: Mono_rev1_GlowDriver.sch

   Programmed for an attiny85
   1MHz internal clock
   - read PIN_RECEIVER signal to turn ON/OFF the glow plug
   - ADC of sensed current
   - I2C to main MCU

                           +-\/-+
                   RESET  1|    |8  VCC   (2.7-5.5V)
    ACS712  (ADC3) Pin 3  2|    |7  Pin 2 (ADC3,SCK) I2C   SCK -> Uno A5
     RADIO  (ADC4) Pin 4  3|    |6  Pin 1 (PWM,MISO) LM2596/LED
                     GND  4|    |5  Pin 0 (PWM,MOSI) I2C   SDA -> Uno A4
                           +----+ 


   */
#define DEBUG

#include "TinyWireS.h"          // "ATTiny85 @ 1Mhz" pour la librairie.
//http://kasey.fr/ATTiny-capteur-universel-en-I2C.html

#define I2C_SLAVE_ADDR  0x26    // On note l'adresse I2C
#define PIN_REGULATOR 1   
#define PIN_RECEIVER 4   

#define TIME_OUT 25000

byte byteRcvd;
boolean driving_glow = false;

void setup()  {
    pinMode(PIN_REGULATOR , OUTPUT);
    pinMode(PIN_RECEIVER  , INPUT);


    TinyWireS.begin(I2C_SLAVE_ADDR);      // on rejoint le bus avec une adresse d'esclave (similaire a la lib wire)
    byteRcvd = 0;
}


void loop(){
    unsigned long duration;
    duration = pulseIn(PIN_RECEIVER, HIGH,TIME_OUT);

    if(duration < 1500){
        driving_glow = true;
        digitalWrite(PIN_REGULATOR, LOW);  
    }
    else{
        driving_glow = false;
        digitalWrite(PIN_REGULATOR, HIGH);
    }

    if (TinyWireS.available()){         // si on revoit quelque chose sur le bus I2C
        byteRcvd = TinyWireS.receive(); // on l'enregistre
#ifdef DEBUG
        Blink();                        // on blink un coup pour montrer que l'on est content
#endif
    }
}

void Blink() {                          // blinker du pauvre :)
    if(driving_glow == false){
        digitalWrite(PIN_REGULATOR,HIGH);
        delay(100);
        digitalWrite(PIN_REGULATOR,LOW);
    }
    else{
        digitalWrite(PIN_REGULATOR,LOW);
        delay(100);
        digitalWrite(PIN_REGULATOR,HIGH);
    }
    
}

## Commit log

2016-06-01 Glow-Driver for RC model engine
    with current sensor / indicator
    [Mono_rev0.brd, Mono_rev0.sch, Mono_rev1_GlowDriver.brd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]
2016-06-01 remove rev0
    Now rev0 is archived, can be remo
    [Mono_rev0.brd, Mono_rev0.sch]
2016-06-02 add main board picture
2016-06-02 add python serial logging sources
    [ENGINE.CSV, LOGGER11.CSV]

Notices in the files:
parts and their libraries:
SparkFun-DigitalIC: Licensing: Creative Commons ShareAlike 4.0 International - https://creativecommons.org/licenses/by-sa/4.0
